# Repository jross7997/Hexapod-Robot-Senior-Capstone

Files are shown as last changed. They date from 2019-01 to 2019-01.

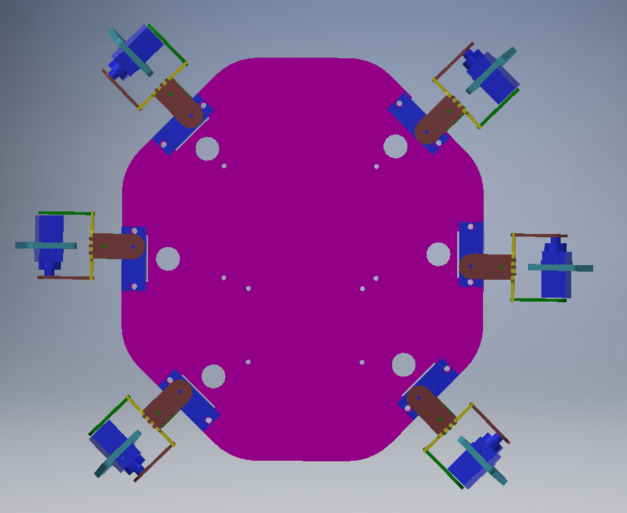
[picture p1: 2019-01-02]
Inventor Parts/Pictures of Parts/RobotTop.PNG

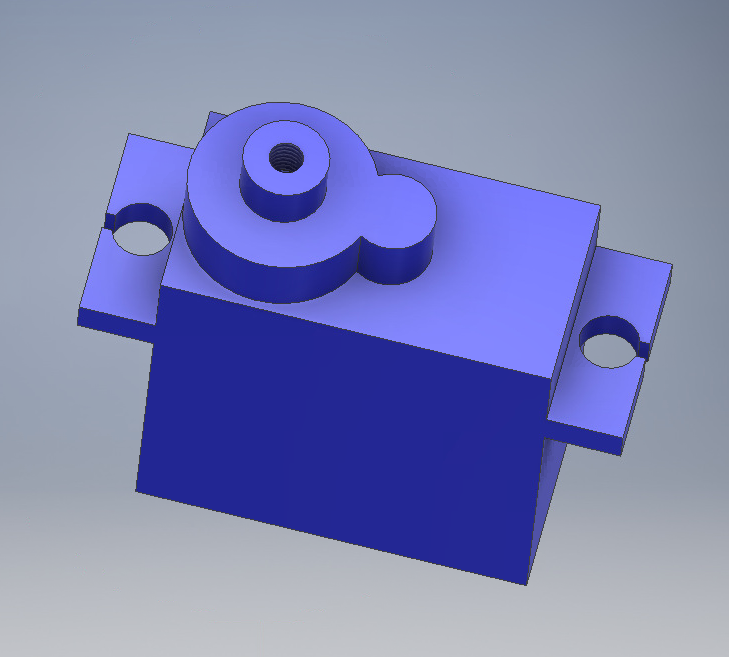
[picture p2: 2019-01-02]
Inventor Parts/Pictures of Parts/servo.PNG

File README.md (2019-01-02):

# Hexapod-Robot-Senior-Capstone
The collection of files created for my group's ECE 492: Capstone Design project

This contains files for the Fall 2018 Capstone Hexapod Walking Robot, built by Kara Fortunato, Justin Ross, and Justin Purtell.

The Projects folder contains the project folders for both the Tiva-C and the Node MCU. The Tiva-C folder is a Code Composer Studio Project.

The Source Code folder just contains the source code for each board. The Tiva-C source code contains a semi-extensive Servo library that was used to abstract away some complexities.

The Inventor Parts folder are all of the Autodesk Inventor parts that were modeled and later used for laser cutting.

The Final_Drawing.dwg is the actual file that a Universal Laser Systems Laser Cutter use to cut the parts.

There are also some instructions on how to connect to the Wifi-board

There was a vote to name it, and as voted on, her name is now Charlotte!
Enjoy!

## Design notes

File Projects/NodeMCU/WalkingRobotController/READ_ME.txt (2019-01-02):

This Code is meant for the NODEMCU 1.0
You need to install the board drivers into the Arduino IDE to get it to compile.
And to write to the NodeMCU, set the baud rate to 115200.

If you want to change the webpage that is displayed, I recommend making changes to the 
index.html file first, and then copying it's contents to the index.h file so that the new 
code is inbetween 
	const char MAIN_page[] PROGMEM = R"=====(
	<!--New/Modified HTML Code -->
	)=====";

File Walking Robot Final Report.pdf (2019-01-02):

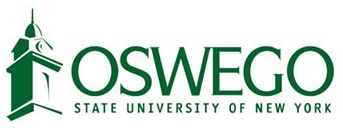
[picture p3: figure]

# SUNY Oswego

# Electrical and Computer Engineering Department

# ECE492

# Hexapod Walking Robot

By

# Kara Fortunato, Justin Ross, and Justin Purtell

## Supervisors

# Rachid Manseur and Marianne Hromalik

Submitted in Partial Fulfillment of the Requirement for the B.Sc. Degree, Electrical and Computer Engineering Department,

# Fall 2018

Project Abstract

Despite large efforts in modern engineering, one fact remains the same when it comes to robotic locomotion: legs and joints will always have a different set of rules than that of a wheeled vehicle when it comes to traversal over flat or rough terrain. A key consideration when designing a “legged” vehicle is how it keeps itself balanced without putting too much weight on one leg and collapsing during motion. In the field of robotics, especially, the ratio between a device’s sense of balance and ability to create forward motion in a way that keeps it grounded is highly important in many respects. The Walking Robot project aims to deliver a device that utilizes these concepts to develop a robot that can maintain its own sense of balance while having several degrees of freedom in movement to walk itself in various directions utilizing a series of controllable legs and joints.

Acknowledgment

All gratitude goes to the ECE department and our fellow colleagues for their advice and support throughout the development process. A special thank you to our advisors Dr. Rachid Manseur and Dr. Marianne Hromalik. Furthermore we would also like to acknowledge Dennis Quill for his involvement and advice.

Student Statement

Throughout the research and development process of this project, the designers, Kara Fortunato, Justin Ross, and Justin Purtell, have applied proper ethics to the design process and in selecting the final proposed design. The designers have held the safety of the public to be paramount and have addressed this in the design in all possible aspects.

Table of Contents

Project Abstract | 2
Acknowledgment | 2
Student Statement | 2
Table of Contents | 3
Figures & Tables List | 4
Problem Statement | 5
Problem Formulation | 5
Project Specifications | 6
Design & Analysis | 7
Number of Legs and Gait | 7
Texas Instruments TM4C123GH6PM | 8
Miuzei SG90 | 10
Individual Pieces of build | 11
NodeMCU V1 | 13
Circuit | 15
Final Build | 17
Standards used | 18
Cost Analysis/Bill of Materials | 18
Hazards & Failure Analysis | 19
ABET Learning Outcome | 20
Conclusions and Discussions | 22
Future Applications: | 22
Future Improvements: | 22
References | 23
Appendices | 24
A-1) Servo Code | 24
A-2) Servo Header File | 33
A-3) Legs Code | 35
A-4) Legs Header File | 41
A-5) UART Code | 42
A-6) UART Header File | 43

A-7) Main Code | 44
A-8) tm4c123gh6pm_startup_ccs.c | 47
A-9) NodeMCU Code | 54
A-10)Index.h | 56
A-11)Laser Cutting Diagram | 60
A-12) Wiring Diagram | 61
A-13) List of Servo to Pin Connections | 61
A-14) TM4C123GH6PM Features | 62
A-15) NodeMCU Specifications | 63
A-16) SG-90 Specifications | 64

Figures & Tables List

Figure 1: An example of the tripod gait | 8
Figure 2: The TM4C123GH6PM (Tiva-C) Microcontroller | 9
Figure 3: A Diagram of the PWM Generators | 9
Figure 4: Miuzei SG90 | 10
Figure 5: Frame Base | 11
Figure 6-8: Servo Mount, Cross-Connection Joint and Leg | 12
Figure 9: Joint and Leg Assembly | 13
Figure 10: The NodeMCU | 14
Figure 11: Web Interface | 14
Figure 12: Wiring Block Diagram | 15
Figure 13: Signal Wiring Diagram | 16
Figure 14: Servo Convention | 16
Figure 15-16: Inventor Assembly Front and Top | 17
Figure 17-19: Final Build Side, Top and Front | 17
Table 1: Student Cost Table
18
Table 2: Total Cost Table | 19

Problem Statement

The objectives of this design are to solve complex problems with robotic locomotion by developing a system in which a robot can walk on its own legs and joints while taking into consideration speed, balance, and aesthetic and ergonomic design.
As defined by a set of goals set by the assigning faculty, the design is also to be constructed of a sturdy material with a customized framework that could help accomplish these considerations with more ease than previous attempts at similar designs. This design is also to take into consideration the adjustments necessary to maintain the robots center of gravity always to allow the robot to balance properly during any direction of movement, as well as at any speed within reason. The customized aspect of this design should also give the robot a clean look about it, where the user should not have to worry about any harm coming to themselves or the robot’s construction while handling or assembling it.
Finally, the robot should be able to be controlled by some outside system where the user can have full control over various commands such as movement forward and backward, turning left or right, as well as any extra commands that can be programmed into the robot simply to make the robot more appealing to the user. This system could consist of an external controller or application that the user could manipulate in some way to achieve a desired command.

Problem Formulation

The issue of robotic movement is a popular topic amongst modern engineers. When you consider new systems that have been recently attempting to automate the workplace and leisure activities, the importance of robotics nowadays has become more paramount than ever. However, the importance of them operating as intended and being safe to operate are key stress factors in robotic design.
The idea of a walking robot has been established on some level within the electronics market already, therefore is an established concept with its own established drawbacks as well when considering scaling them up to a higher level of use. For example, if a working robot were to be used in the workplace, it would most likely be used to establish transport of materials or other product from one point of the building to another destination. This considered, the amount of engineering that must go into this type of product is very advanced because, the robot here not only has to manage to balance under the strain of its own weight; its center of gravity and weight distribution is also affected by any product that the robot may be carrying. Therefore, the necessary amount of design consideration changes considerably. On top of this, the engineer must consider the system that will be used to control the program that robot may run on if it is not entirely autonomous. This fine balance between software development and hardware engineering is part of what makes the field of robotics so complex.
In the case of the Walking Robot project, many of these issues were kept in mind throughout the design process due to the increasing need for these kinds of issues to be considered and solved by skilled engineers. For example, the need for it to balance and carry any weight that it must with the amount of hardware mounted to the frame has to be considered for the robot to perform proper movement. If this device were to be used to transport small goods, for example, this consideration would have to be made to account for the weight of anything it would carry as well to keep its center of gravity consistent with its direction of movement.
The control system of the Walking Robot project also has its own considerations towards these issues. The system that drives the robot should be not only simple enough for the user to operate with ease but, it should also allow as much control over the robot’s specific program as possible to allow the user to operate it accurately and efficiently in its intended application.

Project Specifications

The design of this project consists of many factors, from aspects such as the framework to programming the system to drive the robot’s movement. A strong blend of hardware and software knowledge were implemented to discover an efficient design that would accomplish the intended goals and stay within the constraints specified.
Firstly, the robot needed to be built from custom components that were designed to fit the purpose of the robot itself. The frame of the robot consisted of a series of legs, joints, and a base that could be easily connected and attached together to form the robot. This frame is also designed to house two microcontrollers as well as a series of servo motors that could be used to drive the joints and legs in various directions.

Secondly, a series of programs needed to be developed that could be used to control the servo motors in specific ways such that they could drive the robot in different directions based on how each of the legs and joints coordinated with each other in motion. These programs also take into consideration a method to operate the microcontroller remotely. This program should consist of a series of commands that coordinate with the microcontroller to allow it to activate different operations within the drive program based on user input. These inputs should include, at minimum, a forward drive, backward drive, and rotation left and right, as well as a stop
command. These commands should also have the option to run constantly until the user chooses to stop it.
In short, the agreed upon deliverables are listed below:
1. The robot needs to walk forwards, backwards, and turn left and right
2. The robot needs to maintain balance
3. The body of the robot needs to maintain integrity and look semi-professional

Design & Analysis

Number of Legs and Gait

The first thing that needed to be decided was the number of legs that would be used. There are advantages and disadvantages to each number of legs. For example, two legs would require less hardware than a four legged robot, but balancing on two legs is harder than on four. Since balance was the priority, 6 legs were selected. With a basic Tripod gait, at any given time, at least half of the legs are touching the ground, ensuring a balanced center of gravity. Other gaits for hexapods were considered, like the faster bipod gait, but none of them ensured the same balance that a tripod gait does. The minimum number of degrees of freedom required for a hexapod to use the tripod gait is 12 degrees. This directly translates to the number of servos that are required.

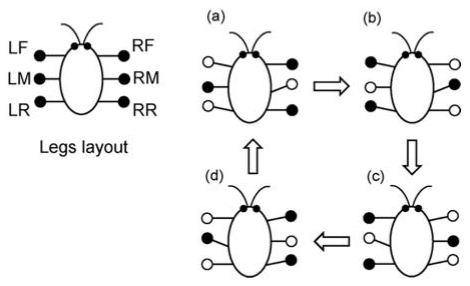
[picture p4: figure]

Figure 1: An example of the tripod gait The forward and backwards follow the Tripod Gait. Which means only three legs move at a time in a triangle shape. The front and back legs of one side along with the middle leg on the opposite side lift up, swing forward, drop down, and finally swing back. When backwards movement is needed, the legs will swing back instead of forward. Turning left and right follows a similar walk cycle. Three legs are on the ground at all times. When turning, the front and back legs swing forward, and the opposite middle leg will lift up and swing back. All three drop down and return back to the neutral standing position. Which way the robot turns is dependent on which sides legs swing forward, and which side swings back.

Texas Instruments TM4C123GH6PM
The microcontroller that was selected to drive the legs on the walking robot was the Texas Instruments TM4C123GH6PM or it was previously called the Tiva-C LaunchPad. The version that was used was still called the Tiva-C LaunchPad, but the new ones are identical. The Tiva-C is based off the 80 MHz ARM Cortex-M4F chipset and has 35 available GPIO pins [2]. It has many available accessories, but the one that was most important to this project was the 16 independent PWM outputs that are generated from two separate PWM modules, each with 4 PWM generators.

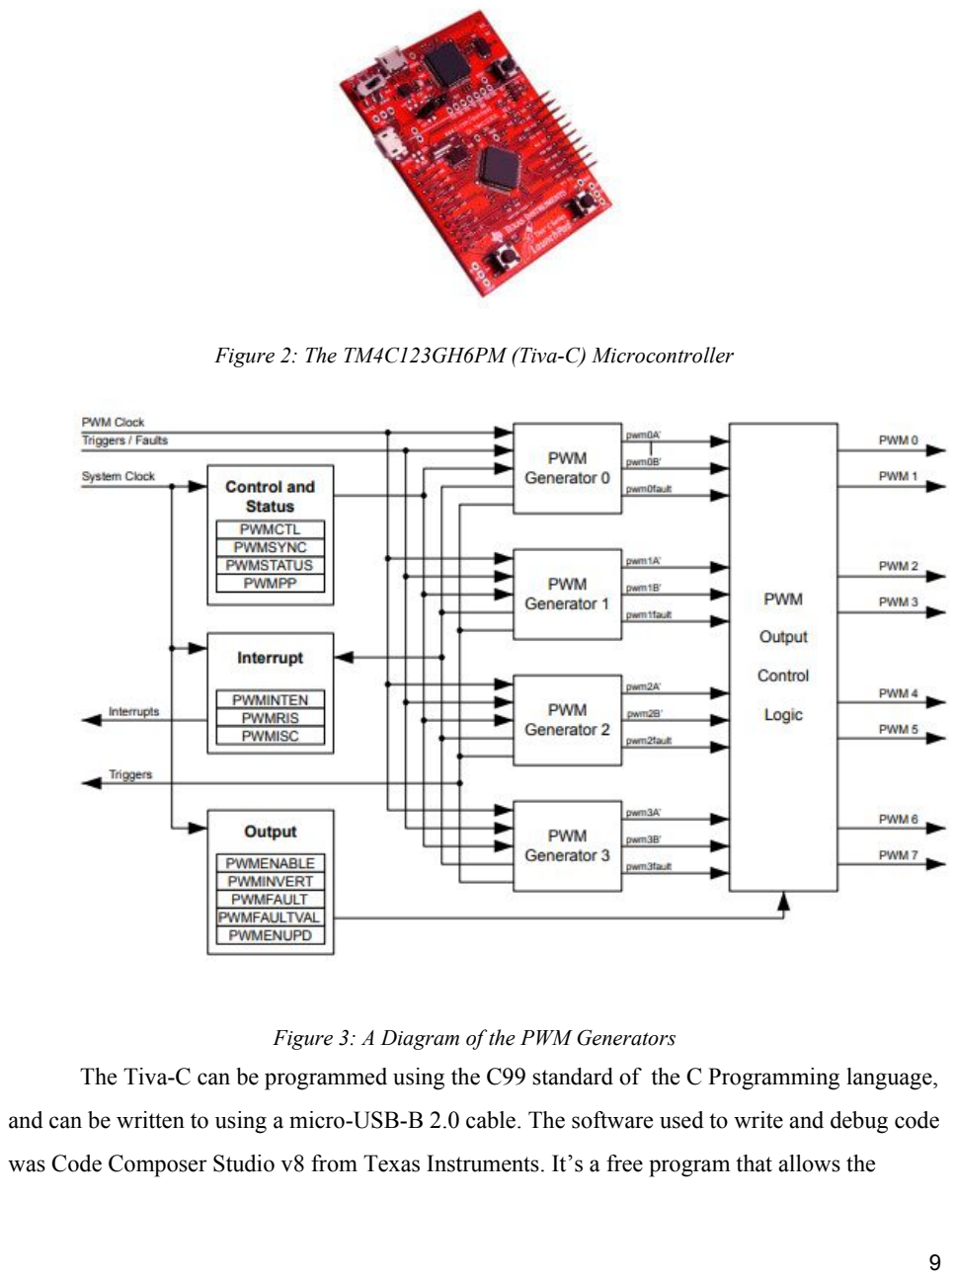
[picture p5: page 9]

Figure 2: The TM4C123GH6PM (Tiva-C) Microcontroller

Figure 3: A Diagram of the PWM Generators The Tiva-C can be programmed using the C99 standard of the C Programming language, and can be written to using a micro-USB-B 2.0 cable. The software used to write and debug code was Code Composer Studio v8 from Texas Instruments. It’s a free program that allows the composition and debugging of code for the Tiva-C, among other Texas Instruments microcontrollers.
Texas Instruments had created a library called “driverlib” that has a variety of register level abstractions that makes programming the Tiva-C a bit easier. Instead of moving individual bits in registers, higher level functions can be called to make the readability of the code easier. But, if necessary, the ability to move individual bits in registers is still available to the user.
The Tiva-C was chosen over other available microcontrollers for two main reasons, versatility and availability. As previously discussed, the Tiva-C has a load of available functions, so the potential for the addition of more features is possible. There was also more than enough PWM pins for the robot. The Tiva-C was also available for free from the ECE department, which helped inform our decision.

Miuzei SG90

It was decided early on that a design goal was to minimize the weight of the walker, so a micro servo form factor was selected. The next thing that was considered was the type of gearing, metal or plastic. The metal gearing is known to be more durable, but they are heavier and more expensive than plastic. Considering this, the Miuzei SG90 micro servos were selected. They have plastic gearing and were lighter and significantly cheaper than the metal counterparts. Twelve SG90’s were used, and they are controlled with a 55 Hz PWM pulse train from the Texas Instruments TM4C123GH6PM microcontroller. The motors have a 120° range of motion, which was more than enough to ensure movement [3].

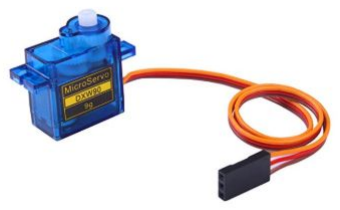
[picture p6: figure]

Figure 4: Miuzei SG90

Individual Pieces of build
The frame is designed using the 3-dimensional computer aided design (CAD) software AutoDesk Inventor. The components are laser-cut from acrylic sheets to ensure that the design was not only pin-point accurate but also sturdy enough to hold up during the next phases. The use of a 3D printer was considered, but it was determined that laser cutting would be a better approach for this project. The ECE department has access to a Universal laser systems laser cutter, making it easy for students to create and cut components without going through a third party. 3D components also cost money according to how long the project takes and how much material is used. Laser cutting has no cost except for the acrylic, which is provided by the department. Additionally, laser cutting is much faster than 3D printing. The entire project takes less than ten minutes to laser cut while a 3D printer might take hours. The fast cutting time allows for models to be adjusted or completely reprinted completely. This is necessary because the robot was completely redesigned several times.
The first part of the frame to be considered was the shape and construction of the base. For this, an octagonal shape is used to allow the robot to consist of 6 legs, 3 on the left side and 3 on the right side, as well as including ports for all the necessary hardware mounting. Holes were made in the base to hold the servos and so that the microcontroller circuit could be mounted.

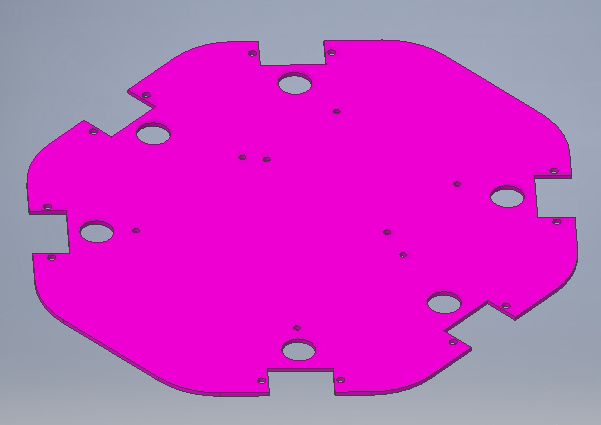
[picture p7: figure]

Figure 5: Frame Base

Next, the legs and joints are designed such that they could hold the servo motors in place and use them for movement while remaining locked to the joints and base by mounting screws and acrylic epoxy. The legs are cut with a concave, pointed “toe” that are coated with a rubber tip such that they could have a strong connection with the ground without slipping. The joints each have cut-out slots that connect each of the joint types to one another. A screw-mounted joint is also used on each side of the servos on the legs and on the base to help lock them in place during movement and keep them connected to the frame.

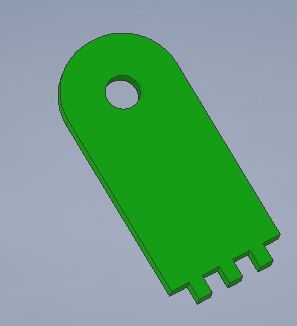
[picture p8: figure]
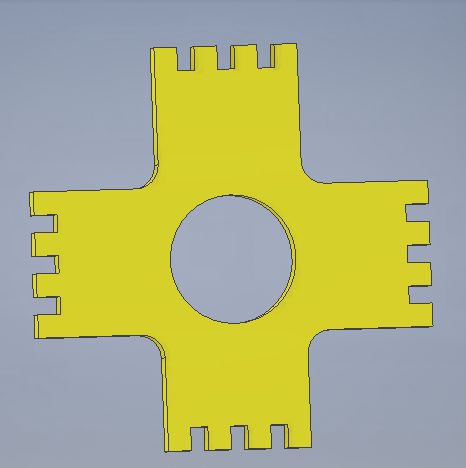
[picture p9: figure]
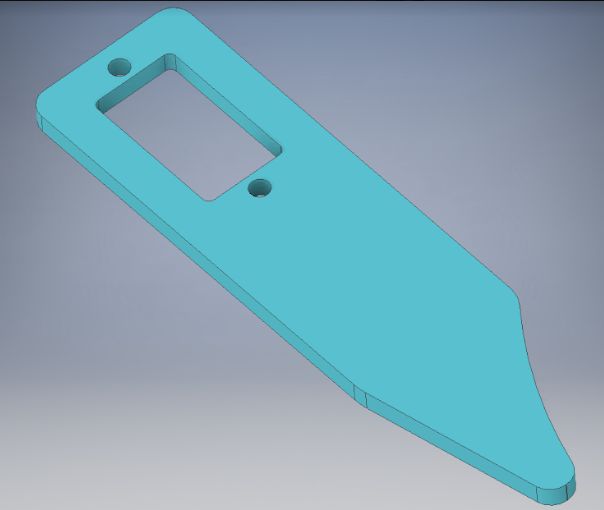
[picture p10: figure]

Figure 6: Servo Mount | Figure 7: Cross Connection Joint | Figure 8: Leg

Once assembled, each leg joint consisted of one cross connection joint, four servo mounts, one leg, and two servos. Each servo was given a number to be referred to. The servo that would be connected to the based was dubbed servo “one” while the servo directly connected to the leg was called servo “two”. This allowed for each servo to be distinguished when the circuit was being built. The final leg joint assembly can be seen in the following figure.

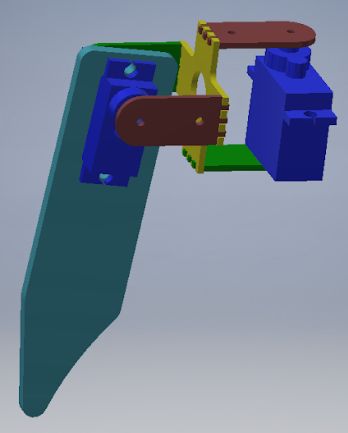
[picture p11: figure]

Figure 9: Joint and Leg Assembly

NodeMCU V1

To control the robot, a method of control needs to be selected. Wireless control was chosen because of accessibility. Anyone with a smart device should be able to have access. To accomplish this, the NodeMCU V1 was used. It is a WiFi-enabled microcontroller that uses the ESP8266MOD chip and can broadcast WiFi in accordance to the IEEE 802.11 b/g/n standard [4]. The NodeMCU has the capability to act as a soft access point that can serve web pages and was programmed using a modified version of C++ in the Arduino IDE. The NodeMCU also supports Lua scripting, but there were issues with the serial connection when the firmware is set for Lua scripting. The only way found to ensure a reliable experience was the use of the Arduino IDE. The NodeMCU was chosen over a Bluetooth module because of the accessibility it provides. Any WiFi enabled device can access and use the walking robot, but a Bluetooth module would require either an OS specific app, or the use of a generic Bluetooth command line.

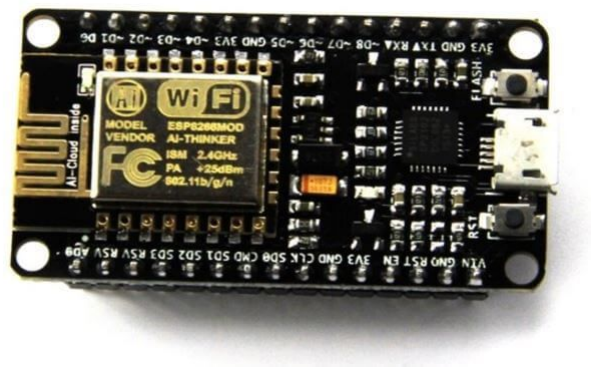
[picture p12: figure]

Figure 10: The NodeMCU
To coordinate with the WiFi module, the program allows the user to connect to the module’s IP address where a web application is loaded that allows the module to communicate with the microcontroller to activate various methods in the servo program based on user command. The application consists of commands including, forward, backward, rotate left, rotate right, stop, wave, continuous operation, and a speed toggle. The web application was written using HTML and AJAX (Asynchronous JavaScript and XML). These commands interact with the TM4C123GH6PM via a UART bridge at a 115200 baud rate, which cause an interrupt, and the previous command is saved to a global variable. Each possible command is mapped to a specific movement function.

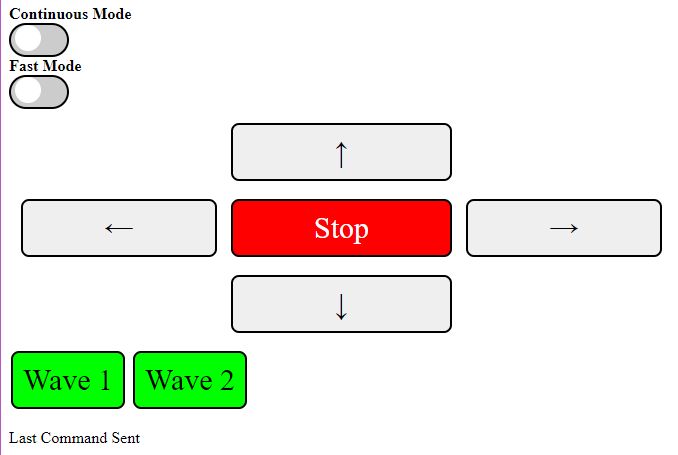
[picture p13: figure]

Figure 11: Web Interface

Circuit

To tie all the components together, a circuit needs to be constructed and soldered together. Each of the twelve servos need to be connected to its respective PWM pin on the Tiva
C. The UART bridge between the Tiva-C and the NodeMCU needs to be put in place. And each of the components need to be powered by an external benchtop power supply. The power supply’s point of entry is the two wires attached to a switch to turn the circuit on or off.

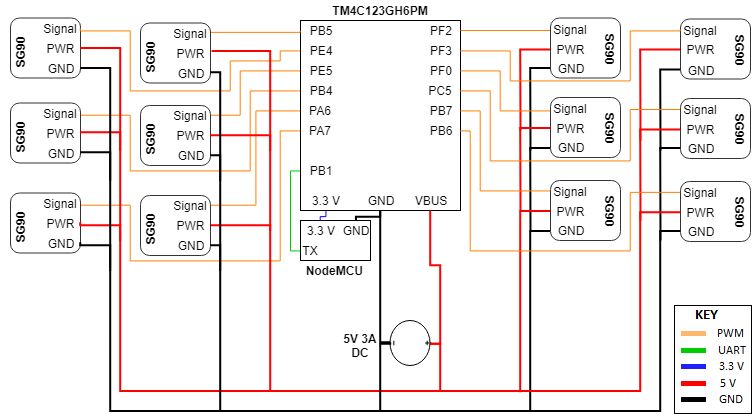
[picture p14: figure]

Figure 12: Wiring Block Diagram

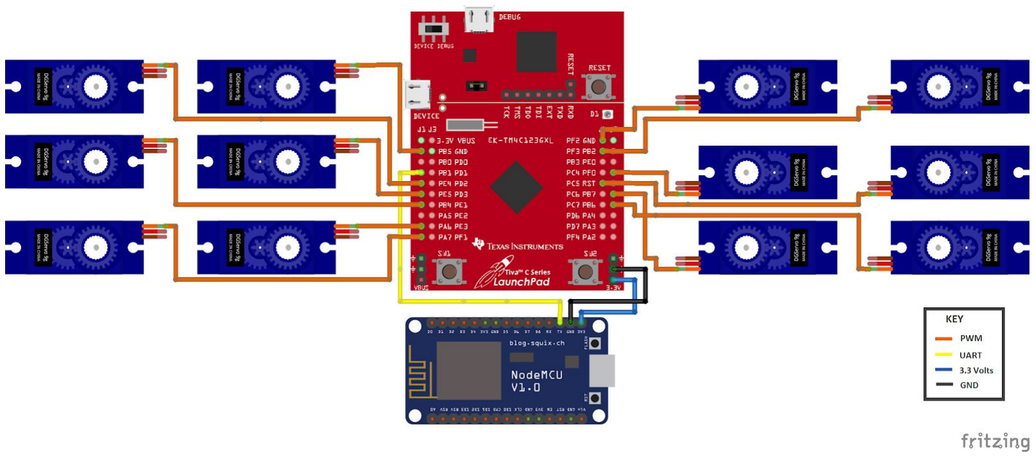
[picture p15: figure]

Figure 13: Signal Wiring Diagram To ensure consistency throughout all aspects of the project, a convention for the legs in terms of the circuit positioning needed to be determined. The base was divided into 3 sections; Front, Middle, and Back. The left side has 6 servos, and the right side has 6 servos. The servos closest to the body are denoted as a servo 1, and the ones on the legs servo 2’s. Knowing what side, left or right, and what third of the base the servo is on, the servo number can quickly be determined. The front needed to be distinct to differentiate the left from the right side and the back from the front. The way that the front was denoted was by the row of googly eyes.

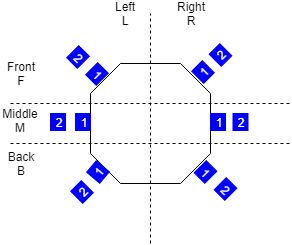
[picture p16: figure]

Figure 14: Servo conventions The physical construction of the circuit was simply done with a 6x8 cm and a 4x6 cm double-sided prototyping PCB. The NodeMCU was placed into soldered female headers on the 4x6 cm board, and the Tiva-C was placed onto soldered male headers on the 6x8cm board. The connections are as shown in the figures above. There were some obstacles that were faced with the soldering, most of which come from inexperience. The biggest issue come from the nature of a solid core wire. Those wires are much more rigid than a braided wire, and are very easy to break.
The final build consisted of six legs and their corresponding joints, as well as one base. Servo “one” is the servo that is directly connected to the base while servo “two” connects to the leg. The final necessary design to be implemented is the mounted PCB. Mounted to the PCB are the WiFi module, the microcontroller, and a switch that can be used to turn the robot on and off. The PCB is then mounted onto the frame’s base using through-hole standoffs of size M2. These components are soldered to the prototyping PCB, as well as each of the PWM ports and WiFi module ports to allow all of the signals to be properly routed to their destinations. To power the robot, a lab bench power supply was set to 5 Volts and 3 Amps and then attached directly to the switch.

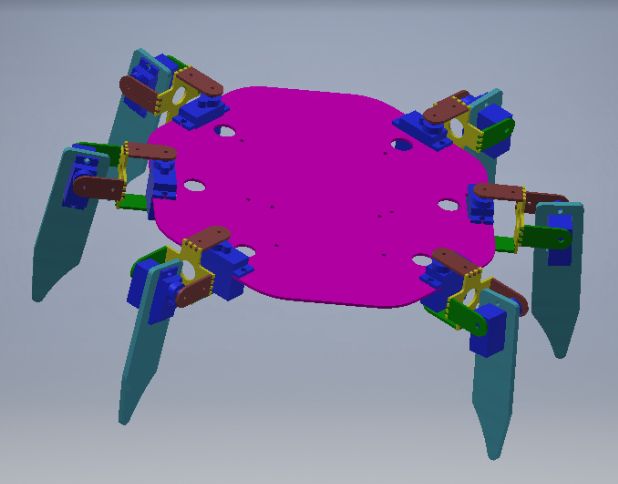
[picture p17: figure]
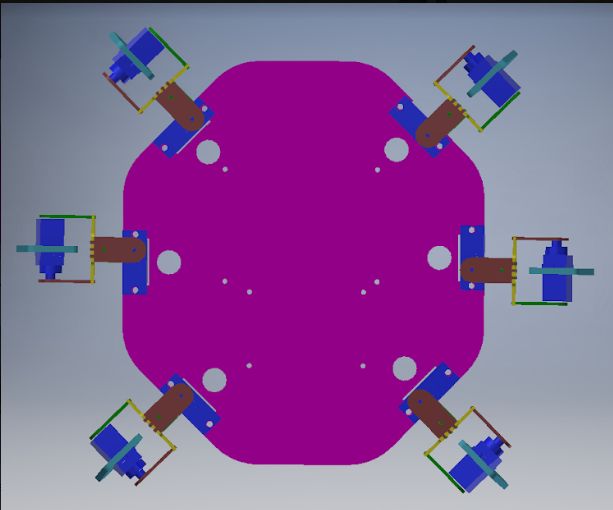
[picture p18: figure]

Figure 15: Inventor Assembly Front | Figure 16: Inventor Assembly Top

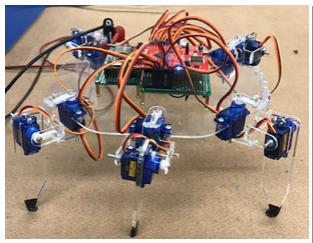
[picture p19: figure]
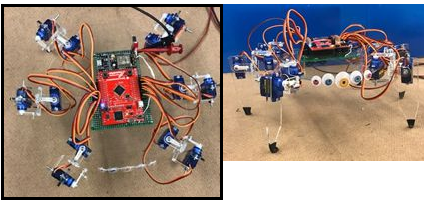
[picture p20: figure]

Figure 17: Final Build (Side) | Figure 18: Final Build (Top) | Figure 19: Final Build (Front)

Standards used
ISO/IEC 9899:1999 for C programming language IEEE 802.11 b/g/n for Wireless Communications Universal Asynchronous Receiver/Transmitter Pulse Width Modulation

Cost Analysis/Bill of Materials

The cost to build the device takes into consideration every individual component and necessary material that was used to complete each step of the design from the planning phase up to the build and testing phases. The total bill of materials used to develop the device is included below.

Table 1: Total Bill of Materials Per-Component

Component/ Material | Quantity | Vendor | Cost ($)
Miuzei SG90 Servo Motors | 12 (+ Extras) | Amazon.com (https://www.amazon.com/Micro-Helicopter-Airplane-Remote-Control/dp/B072V529YD) | 34.58
TM4C123GH6PM Microcontroller | 1 | Mouser (https://www.mouser.com/ProductDetail/Texas-Instruments/EK-TM4C123GXL?qs=TB%2FQ0sBK%2FGefKGr%252bQsiJWQ%3D%3D) | 13.45
Node-MCU V1 Wifi Module | 1 | Amazon.com (https://www.amazon.com/HiLetgo-Internet-Development-Wireless-Micropython/dp/B010O1G1ES?s=electronics) | 8.39
4-40 Machine Bolts and Nuts | 30 each (+ Extras) | Raby’s Ace | 12.44
6 x 8 cm Prototyping PCB | 1 (+ Extras) | Amazon.com (https://www.amazon.com/Double-Side-Prototype-Universal-Printed-Circuit/dp/B0147YM3DG) | 5.99
4 x 6 cm Prototyping PCB | 1(+ Extras) | Amazon.com (https://www.amazon.com/Universal-Protoboard-Prototyping-Printed-Circuit/dp/B06XTPGBS5) | 6.99
M2 Standoff Kit | 1 | Amazon.com (https://www.amazon.com/d/Tile-Spacers/Hilitchi-120pcs-Female-Standoff-Assortment/B018C19KOA) | 8.99
1/16 in Thick 16x24 in Acrylic Sheet | 1 | ePlastics.com (https://www.eplastics.com/sheets/acrylic-plexiglass/plexiglass-acrylic-sheets-clear-SAMPLE-ACRYCLRTHIN-CLEAR) | 8.49
1/8 in Thick 16x24 in Acrylic Sheet | 1 | ePlastics.com (https://www.eplastics.com/SAMPLE-ACRYCLRTHICK-CLEAR) | 21.69
Two-Part Quick Setting Epoxy | 1 | Walmart (https://www.walmart.com/ip/J-B-Weld-50132-PlasticWeld-Quick-Setting-Epoxy-Syringe-Dries-Off-White-25-ml/725449397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) | 5.35
3/8 in Heat Shrink Tubing | 1 | Jameco (https://www.jameco.com/z/FIT-221B-3-8-BK100-VP-Heat-Shrink-Tubing-Fit-221B-3-8-Black-4-Feet-Black-Polyolefin-Tubing_419223.html) | 1.75
Colored Googly Eyes | 1 | Dollar Tree | 1.00
Total Cost | | | 129.11

The total cost to the students with the resources that SUNY Oswego’s ECE Department provides.

Table 2: Total Student Cost Per-Component

Component/ Material | Quantity | Vendor | Cost ($)
Miuzei SG90 Servo Motors | 12 (+ Extras) | Amazon.com (https://www.amazon.com/Micro-Helicopter-Airplane-Remote-Control/dp/B072V529YD) | 34.58
TM4C123GH6PM Microcontroller | 1 | Provided | --
Node-MCU V1 Wifi Module | 1 | Amazon.com (https://www.amazon.com/HiLetgo-Internet-Development-Wireless-Micropython/dp/B010O1G1ES?s=electronics) | 8.39
4-40 Machine Bolts and Nuts | 30 each (+ Extras) | Raby’s Ace | 12.44
6 x 8 cm Prototyping PCB | 1 | Provided | --
4 x 6 cm Prototyping PCB | 1 | Provided | --
M2 Standoff Kit | 1 | Amazon.com (https://www.amazon.com/d/Tile-Spacers/Hilitchi-120pcs-Female-Standoff-Assortment/B018C19KOA) | 8.99
1/16 in Thick 16x24 in Acrylic Sheet | 1 | Provided | --
1/8 in Thick 16x24 in Acrylic Sheet | 1 | Provided | --
Two-Part Quick Setting Epoxy | 1 | Walmart (https://www.walmart.com/ip/J-B-Weld-50132-PlasticWeld-Quick-Setting-Epoxy-Syringe-Dries-Off-White-25-ml/725449397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) | 5.35
3/8 in Heat Shrink Tubing | 1 | Provided | --
Colored Googly Eyes | 1 | Dollar Tree | 1.00
Total Cost | | | 70.75

The operational costs of the walking robot are only that of the cost of electricity that powers the bench power supply.

Hazards & Failure Analysis

As with any solution in development to solve a set of problems, it is the responsibility of the designing engineer to uphold the safety of the public and environment when making any design decision that affects the end-product and how it will be used or perceived by consumers.

Safety was a key feature in the design of the walking robot. There are no sharp edges on the acrylic pieces, and the exposed screws have all be covered with hot glue to prevent any injuries.
The potential for failure is greatest in the joints. Each of the joints is held together with glue, which breaks under high stress.

ABET Learning Outcome

Throughout this project, the take-away from the design process consists of applied knowledge of many of the outcomes outlined by ABET for engineering students required to train as a professional. Various aspects of this design and development process coordinate with these outcomes in many ways.
Engineering Learning Outcomes

### 1. an ability to identify, formulate, and solve complex engineering problems by applying

principles of engineering, science, and mathematics
a. The ECE capstone class is design to get students to identify and solve a problem. In this situation, the problem was to create a walking robot. This was solved using principles and skill involved in math, science, and engineering. These skills included soldering, coding and circuitry among countless others. Without the knowledge gained in classes from the ECE major it would have been nearly impossible to complete this project.
2. an ability to apply engineering design to produce solutions that meet specified needs with consideration of public health, safety, and welfare, as well as global, cultural, social, environmental, and economic factors
a. Several parts of this project could be considered dangerous if not taken care of. For example, a large amount of voltage could be considered dangerous. This robot runs on 5v, a relatively low amount of voltage which is safe for those working with the project. Several screws are sharp and could conflict pain. These screws have been either filed down or had caps put over them to ensure the safety of those near it. The safety of those working on the project and others who may come in contact it was an important of this project and was considered

### 3. an ability to communicate effectively with a range of audiences

a. The ability to communicate with a range of audiences was very important in this project. Not only did the team have to communicate with each other, but reports had to be written at every step which explained the project to those who had no part in it. The group made several reports, including this final report, to explain the project in a manner that can be understood by a large range of audiences.
4. an ability to recognize ethical and professional responsibilities in engineering situations and make informed judgments, which must consider the impact of engineering solutions in global, economic, environmental, and societal contexts
a. This project can be built upon to eventually create a robot that could help the world. However, as the project is now, the ability to make informed judgements considering global and societal contexts was irrelevant.
5. an ability to function effectively on a team whose members together provide leadership, create a collaborative and inclusive environment, establish goals, plan tasks, and meet objectives
a. One of the very first things that was completed on this project was the creation of a task list. This included each step of the process that was to be completed. The use of a task list allowed the group to create and complete goals. The group that designed this robot consisted of three group members. Each group member worked towards one cohesive finished project but took on smaller tasks to get to that goal. For example, one group member was working on the code itself while another soldered together a circuit for the code to run on. This allowed for the project to be completed in a timely manner. The ability to function well on a team and to follow a set task list allowed for the project to be completed effectively.

### 6. an ability to develop and conduct appropriate experimentation, analyze and interpret

data, and use engineering judgment to draw conclusions
a. Experimentation was used at every step of the process in building this robot. The laser printed legs were one part of the project that took a lot of experimentation.

Initially, the legs were very tall with one point at the bottom. This leg was glued to a servo for initial testing. This leg design did not allow the robot to stand on its own because it was too tall and because the single point caused the leg to slip out from underneath the robot. The leg was then modified to hold one servo near the top, and was shortened in length. This allowed a better connection between the leg and the servo. Eventually, after much experimentation and roughly 8 redesign, the leg which is used in the final project was created. The ability to experiment, gather data, and adjust the project accordingly was very important for this project.

### 7. an ability to acquire and apply new knowledge as needed, using appropriate learning

strategies
a. Through code composer labs, the group was able to learn the necessary
commands to program the Tiva-C microcontroller. Other knowledge that may have been needed was requested by faculty or researched separately.

Conclusions and Discussions

The design goal of this walking robot was to walk forward, backward, turn left and right all while keeping its balance. That goal was accomplished, and even expanded upon. For example, the introduction of a WiFi based control system and the two waving functions.

Future Applications:

The design as it currently stands is intended for educational and entertainment uses.

Future Improvements:

1. Time and budget did not permit the inclusion of a battery system to make the system more portable. The use of a battery with a high energy density but a low weight would be ideal, something like a Lithium-Ion or Lithium-Polymer battery pack would work well.
2. Editing the movement methods to make the robot walk more naturally. It currently walks in a very robotic and rigid way. A basic kinematic model could be used to speed up the process of modifying the movement methods.

3. The joints between each servo on the leg are currently held together with glue, which is prone to breaking. A redesign of the joints such that they can be held together with traditional mounting hardware like nuts and bolts would eliminate the problem.

References

[1]B. Baxter, “Tripod-walking Gait,” The Tripod Gait as a Model for Robots. [Online]. Available: https://tripodgaitasamodelforrobots.weebly.com/tripod-walking-gait.html.
[2]“Tiva™ TM4C123GH6PM Microcontroller,” ti.com. [Online]. Available: http://www.ti.com/lit/ds/symlink/tm4c123gh6pm.pdf.
[3]“SG90 Data Sheet.” [Online]. Available: http://www.ee.ic.ac.uk/pcheung/teaching/DE1_EE/stores/sg90_datasheet.pdf.
[4]“NodeMCU ESP8266 ESP-12E WiFi Development Board.” [Online]. Available: https://einstronic.com/wp-content/uploads/2017/06/NodeMCU-ESP8266-ESP-12E-Catalogue.pdf.

Appendices

A-1) Servo Code

*
* servo.c
* Library based off the TIVA C workshop to control the SG90 micro servos *
* Created on: Sep 27, 2018
* Author: jross5
*/

#include <stdint.h>

#include <stdbool.h>

#include "inc/hw_memmap.h" #include "inc/hw_types.h"

#include "driverlib/sysctl.h" #include "driverlib/gpio.h" #include "driverlib/debug.h" #include "driverlib/pwm.h" #include "driverlib/pin_map.h" #include "inc/hw_gpio.h"

#include "driverlib/rom.h"

#define PWM_FREQUENCY 55

uint32_t getPWMFrequency(){
| return PWM_FREQUENCY;
}

void delayMS(uint32_t ms)
{
| SysCtlDelay((SysCtlClockGet() / (3 * 1000)) * ms);
}

uint32_t getPWMClock(){
| return (SysCtlClockGet() / 64);
}

uint32_t getLoad(uint32_t ui32PWMClock, uint32_t ui32PWMFreq){
| return ((ui32PWMClock / ui32PWMFreq) - 1);
}
void PWM_Enable(){
| SysCtlPWMClockSet(SYSCTL_PWMDIV_64); SysCtlPeripheralEnable(SYSCTL_PERIPH_PWM1); SysCtlPeripheralEnable(SYSCTL_PERIPH_PWM0);

}
void GPIOPWM_Enable(){
| SysCtlPeripheralEnable(SYSCTL_PERIPH_GPIOA); SysCtlPeripheralEnable(SYSCTL_PERIPH_GPIOB); SysCtlPeripheralEnable(SYSCTL_PERIPH_GPIOC);

SysCtlPeripheralEnable(SYSCTL_PERIPH_GPIOD); SysCtlPeripheralEnable(SYSCTL_PERIPH_GPIOE); SysCtlPeripheralEnable(SYSCTL_PERIPH_GPIOF);
}

//------------------------------------------------------------------------------------------------------------
//M0 Initilization Methods //-------------------------------------------------------------------------------------------------------------
void M0PWM0_Init(uint32_t ui32Load){
GPIOPinTypePWM(GPIO_PORTB_BASE, GPIO_PIN_6); GPIOPinConfigure(GPIO_PB6_M0PWM0); PWMGenConfigure(PWM0_BASE, PWM_GEN_0, PWM_GEN_MODE_DOWN); PWMGenPeriodSet(PWM0_BASE, PWM_GEN_0, ui32Load); PWMOutputState(PWM0_BASE, PWM_OUT_0_BIT, true); PWMGenEnable(PWM0_BASE, PWM_GEN_0);
}
void M0PWM1_Init(uint32_t ui32Load){ GPIOPinTypePWM(GPIO_PORTB_BASE, GPIO_PIN_7); GPIOPinConfigure(GPIO_PB7_M0PWM1); PWMGenConfigure(PWM0_BASE, PWM_GEN_0, PWM_GEN_MODE_DOWN); PWMGenPeriodSet(PWM0_BASE, PWM_GEN_0, ui32Load); PWMOutputState(PWM0_BASE, PWM_OUT_1_BIT, true); PWMGenEnable(PWM0_BASE, PWM_GEN_0);
}
void M0PWM2_Init(uint32_t ui32Load){ GPIOPinTypePWM(GPIO_PORTB_BASE, GPIO_PIN_4); GPIOPinConfigure(GPIO_PB4_M0PWM2); PWMGenConfigure(PWM0_BASE, PWM_GEN_1, PWM_GEN_MODE_DOWN); PWMGenPeriodSet(PWM0_BASE, PWM_GEN_1, ui32Load); PWMOutputState(PWM0_BASE, PWM_OUT_2_BIT, true); PWMGenEnable(PWM0_BASE, PWM_GEN_1);
}
void M0PWM3_Init(uint32_t ui32Load){ GPIOPinTypePWM(GPIO_PORTB_BASE, GPIO_PIN_5); GPIOPinConfigure(GPIO_PB5_M0PWM3); PWMGenConfigure(PWM0_BASE, PWM_GEN_1, PWM_GEN_MODE_DOWN); PWMGenPeriodSet(PWM0_BASE, PWM_GEN_1, ui32Load); PWMOutputState(PWM0_BASE, PWM_OUT_3_BIT, true); PWMGenEnable(PWM0_BASE, PWM_GEN_1);
}
void M0PWM4_Init(uint32_t ui32Load){ GPIOPinTypePWM(GPIO_PORTE_BASE, GPIO_PIN_4); GPIOPinConfigure(GPIO_PE4_M0PWM4); PWMGenConfigure(PWM0_BASE, PWM_GEN_2, PWM_GEN_MODE_DOWN); PWMGenPeriodSet(PWM0_BASE, PWM_GEN_2, ui32Load); PWMOutputState(PWM0_BASE, PWM_OUT_4_BIT, true); PWMGenEnable(PWM0_BASE, PWM_GEN_2);
}
void M0PWM5_Init(uint32_t ui32Load){ GPIOPinTypePWM(GPIO_PORTE_BASE, GPIO_PIN_5); GPIOPinConfigure(GPIO_PE5_M0PWM5); PWMGenConfigure(PWM0_BASE, PWM_GEN_2, PWM_GEN_MODE_DOWN);

PWMGenPeriodSet(PWM0_BASE, PWM_GEN_2, ui32Load); PWMOutputState(PWM0_BASE, PWM_OUT_5_BIT, true); PWMGenEnable(PWM0_BASE, PWM_GEN_2);
}
void M0PWM6_Init(uint32_t ui32Load){ GPIOPinTypePWM(GPIO_PORTC_BASE, GPIO_PIN_4); GPIOPinConfigure(GPIO_PC4_M0PWM6); PWMGenConfigure(PWM0_BASE, PWM_GEN_3, PWM_GEN_MODE_DOWN); PWMGenPeriodSet(PWM0_BASE, PWM_GEN_3, ui32Load); PWMOutputState(PWM0_BASE, PWM_OUT_6_BIT, true); PWMGenEnable(PWM0_BASE, PWM_GEN_3);
}
void M0PWM7_Init(uint32_t ui32Load){ GPIOPinTypePWM(GPIO_PORTC_BASE, GPIO_PIN_5); GPIOPinConfigure(GPIO_PC5_M0PWM7); PWMGenConfigure(PWM0_BASE, PWM_GEN_3, PWM_GEN_MODE_DOWN); PWMGenPeriodSet(PWM0_BASE, PWM_GEN_3, ui32Load); PWMOutputState(PWM0_BASE, PWM_OUT_7_BIT, true);
PWMGenEnable(PWM0_BASE, PWM_GEN_3);
}

//------------------------------------------------------------------------------------------------------------
//M1 Initilization Methods //-------------------------------------------------------------------------------------------------------------
void M1PWM0_Init(uint32_t ui32Load){
GPIOPinTypePWM(GPIO_PORTD_BASE, GPIO_PIN_0); GPIOPinConfigure(GPIO_PD0_M1PWM0); PWMGenConfigure(PWM1_BASE, PWM_GEN_0, PWM_GEN_MODE_DOWN); PWMGenPeriodSet(PWM1_BASE, PWM_GEN_0, ui32Load); PWMOutputState(PWM1_BASE, PWM_OUT_0_BIT, true); PWMGenEnable(PWM1_BASE, PWM_GEN_0);
}
void M1PWM1_Init(uint32_t ui32Load){ GPIOPinTypePWM(GPIO_PORTD_BASE, GPIO_PIN_1); GPIOPinConfigure(GPIO_PD1_M1PWM1); PWMGenConfigure(PWM1_BASE, PWM_GEN_0, PWM_GEN_MODE_DOWN); PWMGenPeriodSet(PWM1_BASE, PWM_GEN_0, ui32Load); PWMOutputState(PWM1_BASE, PWM_OUT_1_BIT, true); PWMGenEnable(PWM1_BASE, PWM_GEN_0);
}
void M1PWM2_Init(uint32_t ui32Load){ GPIOPinTypePWM(GPIO_PORTA_BASE, GPIO_PIN_6); GPIOPinConfigure(GPIO_PA6_M1PWM2); PWMGenConfigure(PWM1_BASE, PWM_GEN_1, PWM_GEN_MODE_DOWN); PWMGenPeriodSet(PWM1_BASE, PWM_GEN_1, ui32Load); PWMOutputState(PWM1_BASE, PWM_OUT_2_BIT, true); PWMGenEnable(PWM1_BASE, PWM_GEN_1);
}
void M1PWM3_Init(uint32_t ui32Load){ GPIOPinTypePWM(GPIO_PORTA_BASE, GPIO_PIN_7); GPIOPinConfigure(GPIO_PA7_M1PWM3); PWMGenConfigure(PWM1_BASE, PWM_GEN_1, PWM_GEN_MODE_DOWN);

PWMGenPeriodSet(PWM1_BASE, PWM_GEN_1, ui32Load); PWMOutputState(PWM1_BASE, PWM_OUT_3_BIT, true); PWMGenEnable(PWM1_BASE, PWM_GEN_1);
}
void M1PWM4_Init(uint32_t ui32Load){ GPIOPinTypePWM(GPIO_PORTF_BASE, GPIO_PIN_0); GPIOPinConfigure(GPIO_PF0_M1PWM4); PWMGenConfigure(PWM1_BASE, PWM_GEN_2, PWM_GEN_MODE_DOWN); PWMGenPeriodSet(PWM1_BASE, PWM_GEN_2, ui32Load); PWMOutputState(PWM1_BASE, PWM_OUT_4_BIT, true); PWMGenEnable(PWM1_BASE, PWM_GEN_2);
}
void M1PWM5_Init(uint32_t ui32Load){ GPIOPinTypePWM(GPIO_PORTF_BASE, GPIO_PIN_1); GPIOPinConfigure(GPIO_PF1_M1PWM5); PWMGenConfigure(PWM1_BASE, PWM_GEN_2, PWM_GEN_MODE_DOWN); PWMGenPeriodSet(PWM1_BASE, PWM_GEN_2, ui32Load); PWMOutputState(PWM1_BASE, PWM_OUT_5_BIT, true); PWMGenEnable(PWM1_BASE, PWM_GEN_2);
}
void M1PWM6_Init(uint32_t ui32Load){ GPIOPinTypePWM(GPIO_PORTF_BASE, GPIO_PIN_2); GPIOPinConfigure(GPIO_PF2_M1PWM6); PWMGenConfigure(PWM1_BASE, PWM_GEN_3, PWM_GEN_MODE_DOWN); PWMGenPeriodSet(PWM1_BASE, PWM_GEN_3, ui32Load); PWMOutputState(PWM1_BASE, PWM_OUT_6_BIT, true); PWMGenEnable(PWM1_BASE, PWM_GEN_3);
}
void M1PWM7_Init(uint32_t ui32Load){ GPIOPinTypePWM(GPIO_PORTF_BASE, GPIO_PIN_3); GPIOPinConfigure(GPIO_PF3_M1PWM7); PWMGenConfigure(PWM1_BASE, PWM_GEN_3, PWM_GEN_MODE_DOWN); PWMGenPeriodSet(PWM1_BASE, PWM_GEN_3, ui32Load); PWMOutputState(PWM1_BASE, PWM_OUT_7_BIT, true);
PWMGenEnable(PWM1_BASE, PWM_GEN_3);
}
//------------------------------------------------------------------------------------------------------------
//M0 Position Methods
//-------------------------------------------------------------------------------------------------------------
//M0 PWM0 Pin PB6 position method
void M0PWM0_PositionServo(uint8_t ui8Degrees, uint32_t ui32Load) // Servo position from 0 to 120 degrees
{
uint8_t ui8Adjust;

if (ui8Degrees > 120)
{
ui8Adjust = 140;
}
else
{
ui8Adjust = 56.0 + ((float) ui8Degrees * (140.0 - 56.0)) / 120.0;

}
PWMPulseWidthSet(PWM0_BASE, PWM_OUT_0, ui8Adjust * ui32Load / 1000); }

//M0 PWM1 Pin PB7 position method
void M0PWM1_PositionServo(uint8_t ui8Degrees, uint32_t ui32Load) // Servo position from 0 to 120 degrees
{
uint8_t ui8Adjust;

if (ui8Degrees > 120)
{
ui8Adjust = 140;
}
else
{
ui8Adjust = 56.0 + ((float) ui8Degrees * (140.0 - 56.0)) / 120.0; }
PWMPulseWidthSet(PWM0_BASE, PWM_OUT_1, ui8Adjust * ui32Load / 1000); }

//M0 PWM2 Pin PB4 position method
void M0PWM2_PositionServo(uint8_t ui8Degrees, uint32_t ui32Load) // Servo position from 0 to 120 degrees
{
uint8_t ui8Adjust;

if (ui8Degrees > 120)
{
ui8Adjust = 140;
}
else
{
ui8Adjust = 56.0 + ((float) ui8Degrees * (140.0 - 56.0)) / 120.0; }
PWMPulseWidthSet(PWM0_BASE, PWM_OUT_2, ui8Adjust * ui32Load / 1000); }
//M0 PWM3 Pin PB5 position method
void M0PWM3_PositionServo(uint8_t ui8Degrees, uint32_t ui32Load) // Servo position from 0 to 120 degrees
{
uint8_t ui8Adjust;

if (ui8Degrees > 120)
{
ui8Adjust = 140;
}
else
{
ui8Adjust = 56.0 + ((float) ui8Degrees * (140.0 - 56.0)) / 120.0; }
PWMPulseWidthSet(PWM0_BASE, PWM_OUT_3, ui8Adjust * ui32Load / 1000); }
//M0 PWM4 Pin PE4 position method void M0PWM4_PositionServo(uint8_t ui8Degrees, uint32_t ui32Load) // Servo position from 0 to 120 degrees
{
uint8_t ui8Adjust;

if (ui8Degrees > 120)
{
ui8Adjust = 140;
}
else
{
ui8Adjust = 56.0 + ((float) ui8Degrees * (140.0 - 56.0)) / 120.0; }
PWMPulseWidthSet(PWM0_BASE, PWM_OUT_4, ui8Adjust * ui32Load / 1000); }
//M0 PWM5 Pin PE5 position method
void M0PWM5_PositionServo(uint8_t ui8Degrees, uint32_t ui32Load) // Servo position from 0 to 120 degrees
{
uint8_t ui8Adjust;

if (ui8Degrees > 120)
{
ui8Adjust = 140;
}
else
{
ui8Adjust = 56.0 + ((float) ui8Degrees * (140.0 - 56.0)) / 120.0; }
PWMPulseWidthSet(PWM0_BASE, PWM_OUT_5, ui8Adjust * ui32Load / 1000); }
//M0 PWM6 Pin PC4 position method
void M0PWM6_PositionServo(uint8_t ui8Degrees, uint32_t ui32Load) // Servo position from 0 to 120 degrees
{
uint8_t ui8Adjust;

if (ui8Degrees > 120)
{
ui8Adjust = 140;
}
else
{
ui8Adjust = 56.0 + ((float) ui8Degrees * (140.0 - 56.0)) / 120.0; }
PWMPulseWidthSet(PWM0_BASE, PWM_OUT_6, ui8Adjust * ui32Load / 1000); }
//M0 PWM7 Pin PC5 position method
void M0PWM7_PositionServo(uint8_t ui8Degrees, uint32_t ui32Load) // Servo position from 0 to 120 degrees
{
uint8_t ui8Adjust;

if (ui8Degrees > 120)

{
ui8Adjust = 140;
}
else
{
ui8Adjust = 56.0 + ((float) ui8Degrees * (140.0 - 56.0)) / 120.0; }
PWMPulseWidthSet(PWM0_BASE, PWM_OUT_7, ui8Adjust * ui32Load / 1000);
}

//------------------------------------------------------------------------------------------------------------
//M1 Position Methods
//-------------------------------------------------------------------------------------------------------------
//M1 PWM0 Pin PD0 position method
void M1PWM0_PositionServo(uint8_t ui8Degrees, uint32_t ui32Load) // Servo position from 0 to 120 degrees
{
uint8_t ui8Adjust;

if (ui8Degrees > 120)
{
ui8Adjust = 140;
}
else
{
ui8Adjust = 56.0 + ((float) ui8Degrees * (140.0 - 56.0)) / 120.0; }
PWMPulseWidthSet(PWM1_BASE, PWM_OUT_0, ui8Adjust * ui32Load / 1000); }

//M1 PWM1 Pin PD1 position method
void M1PWM1_PositionServo(uint8_t ui8Degrees, uint32_t ui32Load) // Servo position from 0 to 120 degrees
{
uint8_t ui8Adjust;

if (ui8Degrees > 120)
{
ui8Adjust = 140;
}
else
{
ui8Adjust = 56.0 + ((float) ui8Degrees * (140.0 - 56.0)) / 120.0; }
PWMPulseWidthSet(PWM1_BASE, PWM_OUT_1, ui8Adjust * ui32Load / 1000); }

//M1 PWM2 Pin PA6 position method
void M1PWM2_PositionServo(uint8_t ui8Degrees, uint32_t ui32Load) // Servo position from 0 to 120 degrees
{
uint8_t ui8Adjust;

if (ui8Degrees > 120)
{
ui8Adjust = 140;
}
else
{
ui8Adjust = 56.0 + ((float) ui8Degrees * (140.0 - 56.0)) / 120.0; }
PWMPulseWidthSet(PWM1_BASE, PWM_OUT_2, ui8Adjust * ui32Load / 1000); }
//M1 PWM3 Pin PA7 position method
void M1PWM3_PositionServo(uint8_t ui8Degrees, uint32_t ui32Load) // Servo position from 0 to 120 degrees
{
uint8_t ui8Adjust;

if (ui8Degrees > 120)
{
ui8Adjust = 140;
}
else
{
ui8Adjust = 56.0 + ((float) ui8Degrees * (140.0 - 56.0)) / 120.0; }
PWMPulseWidthSet(PWM1_BASE, PWM_OUT_3, ui8Adjust * ui32Load / 1000); }
//M1 PWM4 Pin PF0 position method
void M1PWM4_PositionServo(uint8_t ui8Degrees, uint32_t ui32Load) // Servo position from 0 to 120 degrees
{
uint8_t ui8Adjust;

if (ui8Degrees > 120)
{
ui8Adjust = 140;
}
else
{
ui8Adjust = 56.0 + ((float) ui8Degrees * (140.0 - 56.0)) / 120.0; }
PWMPulseWidthSet(PWM1_BASE, PWM_OUT_4, ui8Adjust * ui32Load / 1000); }
//M1 PWM5 Pin PF1 position method
void M1PWM5_PositionServo(uint8_t ui8Degrees, uint32_t ui32Load) // Servo position from 0 to 120 degrees
{
uint8_t ui8Adjust;

if (ui8Degrees > 120)
{
ui8Adjust = 140;
}
else

{
ui8Adjust = 56.0 + ((float) ui8Degrees * (140.0 - 56.0)) / 120.0; }
PWMPulseWidthSet(PWM1_BASE, PWM_OUT_5, ui8Adjust * ui32Load / 1000); }
//M1 PWM6 Pin PF2 position method
void M1PWM6_PositionServo(uint8_t ui8Degrees, uint32_t ui32Load) // Servo position from 0 to 120 degrees
{
uint8_t ui8Adjust;

if (ui8Degrees > 120)
{
ui8Adjust = 140;
}
else
{
ui8Adjust = 56.0 + ((float) ui8Degrees * (140.0 - 56.0)) / 120.0; }
PWMPulseWidthSet(PWM1_BASE, PWM_OUT_6, ui8Adjust * ui32Load / 1000); }
//M1 PWM7 Pin PF3 position method
void M1PWM7_PositionServo(uint8_t ui8Degrees, uint32_t ui32Load) // Servo position from 0 to 120 degrees
{
uint8_t ui8Adjust;

if (ui8Degrees > 120)
{
ui8Adjust = 140;
}
else
{
ui8Adjust = 56.0 + ((float) ui8Degrees * (140.0 - 56.0)) / 120.0; }
PWMPulseWidthSet(PWM1_BASE, PWM_OUT_7, ui8Adjust * ui32Load / 1000); }

A-2) Servo Header File

/*
* servo.h
*
* Created on: Sep 27, 2018
* | Author: jross5
*/

#ifndef SERVO_H_

#define SERVO_H_

extern void delayMS(uint32_t ms);

extern uint32_t getPWMFrequency();
extern uint32_t getPWMClock();
extern uint32_t getLoad(uint32_t ui32PWMClock, uint32_t ui32PWMFreq);

extern void PWM_Enable();
extern void GPIOPWM_Enable();

extern void M0PWM0_Init(uint32_t ui32Load); extern void M0PWM1_Init(uint32_t ui32Load); extern void M0PWM2_Init(uint32_t ui32Load); extern void M0PWM3_Init(uint32_t ui32Load); extern void M0PWM4_Init(uint32_t ui32Load); extern void M0PWM5_Init(uint32_t ui32Load); extern void M0PWM6_Init(uint32_t ui32Load); extern void M0PWM7_Init(uint32_t ui32Load);

extern void M1PWM0_Init(uint32_t ui32Load); extern void M1PWM1_Init(uint32_t ui32Load); extern void M1PWM2_Init(uint32_t ui32Load); extern void M1PWM3_Init(uint32_t ui32Load); extern void M1PWM4_Init(uint32_t ui32Load); extern void M1PWM5_Init(uint32_t ui32Load);
extern void M1PWM6_Init(uint32_t ui32Load);
extern void M1PWM7_Init(uint32_t ui32Load);

extern void M0PWM0_PositionServo(uint8_t ui8Degrees, uint32_t ui32Load); extern void M0PWM1_PositionServo(uint8_t ui8Degrees, uint32_t ui32Load); extern void M0PWM2_PositionServo(uint8_t ui8Degrees, uint32_t ui32Load); extern void M0PWM3_PositionServo(uint8_t ui8Degrees, uint32_t ui32Load); extern void M0PWM4_PositionServo(uint8_t ui8Degrees, uint32_t ui32Load); extern void M0PWM5_PositionServo(uint8_t ui8Degrees, uint32_t ui32Load); extern void M0PWM6_PositionServo(uint8_t ui8Degrees, uint32_t ui32Load); extern void M0PWM7_PositionServo(uint8_t ui8Degrees, uint32_t ui32Load);

extern void M1PWM0_PositionServo(uint8_t ui8Degrees, uint32_t ui32Load); extern void M1PWM1_PositionServo(uint8_t ui8Degrees, uint32_t ui32Load); extern void M1PWM2_PositionServo(uint8_t ui8Degrees, uint32_t ui32Load); extern void M1PWM3_PositionServo(uint8_t ui8Degrees, uint32_t ui32Load);

extern void M1PWM4_PositionServo(uint8_t ui8Degrees, uint32_t ui32Load); extern void M1PWM5_PositionServo(uint8_t ui8Degrees, uint32_t ui32Load); extern void M1PWM6_PositionServo(uint8_t ui8Degrees, uint32_t ui32Load); extern void M1PWM7_PositionServo(uint8_t ui8Degrees, uint32_t ui32Load);

#endif /* SERVO_H_ */

A-3) Legs Code

/*
* legs.c
* Library based off the servo.c that abstracts the control of servos * Created on: Oct 9, 2018
* | Author: jross5
*/

#include <stdint.h>

#include <stdbool.h>

#include "inc/hw_memmap.h" #include "inc/hw_types.h"

#include "driverlib/sysctl.h" #include "driverlib/gpio.h" #include "driverlib/debug.h" #include "driverlib/pwm.h" #include "driverlib/pin_map.h" #include "inc/hw_gpio.h"

#include "driverlib/rom.h"

#include "servo.h"

//------------------------------------------------------------------------------------
//INITIALIZATION METHODS
//------------------------------------------------------------------------------------

//Initialize each PWM pin
void All_PWM_Init(){
uint32_t ui32PWM_Freq = getPWMFrequency(); GPIOPWM_Enable();
PWM_Enable();

// Unlock the Pin PF0 and Set the Commit Bit HWREG(GPIO_PORTF_BASE + GPIO_O_LOCK) = GPIO_LOCK_KEY; HWREG(GPIO_PORTF_BASE + GPIO_O_CR) |= 0x01;

uint32_t ui32PWMClock = getPWMClock();
uint32_t ui32Load = getLoad(ui32PWMClock, ui32PWM_Freq);

M0PWM0_Init(ui32Load); //PB6
M0PWM1_Init(ui32Load); //PB7
M0PWM2_Init(ui32Load); //PB4
M0PWM3_Init(ui32Load); //PB5 M0PWM4_Init(ui32Load); //PE4 M0PWM5_Init(ui32Load); //PE5 M0PWM6_Init(ui32Load); //PC4 M0PWM7_Init(ui32Load); //PC5

M1PWM0_Init(ui32Load); //PD0 M1PWM1_Init(ui32Load); //PD1

M1PWM2_Init(ui32Load); //PA6 M1PWM3_Init(ui32Load); //PA7 M1PWM4_Init(ui32Load); //PF0 M1PWM5_Init(ui32Load); //PF1 M1PWM6_Init(ui32Load); //PF2 M1PWM7_Init(ui32Load); //PF3
}

//Initialize each pin used for the hex's Legs void Legs_Init(uint32_t ui32Load){ GPIOPWM_Enable();
PWM_Enable();
// Unlock the Pin PF0 and Set the Commit Bit HWREG(GPIO_PORTF_BASE + GPIO_O_LOCK) = GPIO_LOCK_KEY; HWREG(GPIO_PORTF_BASE + GPIO_O_CR) |= 0x01;

M0PWM0_Init(ui32Load); //PB6
M0PWM1_Init(ui32Load); //PB7
M0PWM2_Init(ui32Load); //PB4 M0PWM3_Init(ui32Load); //PB5 M0PWM4_Init(ui32Load); //PE4 M0PWM5_Init(ui32Load); //PE5 M0PWM7_Init(ui32Load); //PC5

M1PWM2_Init(ui32Load); //PA6 M1PWM3_Init(ui32Load); //PA7 M1PWM4_Init(ui32Load); //PF0 M1PWM6_Init(ui32Load); //PF2 M1PWM7_Init(ui32Load); //PF3

}

//------------------------------------------------------------------------------------
//LEFT LEG POSITION METHODS //------------------------------------------------------------------------------------

//Front Left Leg position method
//L1F - pin PB5
//L2F - pin PE4
void LegLF_Position(uint8_t ui8L1Degrees,uint8_t ui8L2Degrees,uint32_t ui32Load){
M0PWM3_PositionServo(ui8L1Degrees, ui32Load); M0PWM4_PositionServo(ui8L2Degrees, ui32Load);
}
//Middle Left Leg position method
//L1M - pin PE5
//L2M - pin PB4
void LegLM_Position(uint8_t ui8L1Degrees,uint8_t ui8L2Degrees,uint32_t ui32Load){
M0PWM5_PositionServo(ui8L1Degrees, ui32Load); M0PWM2_PositionServo(ui8L2Degrees, ui32Load);
}

//Back Left Leg position method
//L1B - pin PA6
//L2B - pin PA7
void LegLB_Position(uint8_t ui8L1Degrees,uint8_t ui8L2Degrees,uint32_t ui32Load){
M1PWM2_PositionServo(ui8L1Degrees, ui32Load); M1PWM3_PositionServo(ui8L2Degrees, ui32Load);
}

//------------------------------------------------------------------------------------
//RIGHT LEG POSITION METHODS //------------------------------------------------------------------------------------

//Front Right Leg position method
//R1F - pin PF2
//R2F - pin PF3
void LegRF_Position(uint8_t ui8R1Degrees,uint8_t ui8R2Degrees,uint32_t ui32Load){
M1PWM6_PositionServo(ui8R1Degrees, ui32Load); M1PWM7_PositionServo(ui8R2Degrees, ui32Load);
}
//Middle Right Leg position method
//R1M - pin PF0
//R2M - pin PC5
void LegRM_Position(uint8_t ui8R1Degrees,uint8_t ui8R2Degrees,uint32_t ui32Load){
M1PWM4_PositionServo(ui8R1Degrees, ui32Load); M0PWM7_PositionServo(ui8R2Degrees, ui32Load);
}
//Back right Leg position method
//R1B - pin PB7
//R2B - pin PB6
void LegRB_Position(uint8_t ui8R1Degrees,uint8_t ui8R2Degrees,uint32_t ui32Load){
M0PWM1_PositionServo(ui8R1Degrees, ui32Load); M0PWM0_PositionServo(ui8R2Degrees, ui32Load);
}

//------------------------------------------------------------------------------------
// Custom Position Methods //------------------------------------------------------------------------------------
//Set every servos on body to 60 and servos on legs to 0 degrees. Standing neutrally
void Neutral_Stance(uint32_t ui32Load){
LegLF_Position(60,0,ui32Load);
LegLM_Position(60,0,ui32Load); LegLB_Position(60,0,ui32Load);

LegRF_Position(60,0,ui32Load); LegRM_Position(60,0,ui32Load);

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
A-4) Legs Header File

/*
* legs.h
*
* Created on: Oct 9, 2018
* | Author: jross5
*/

#ifndef LEGS_H_

#define LEGS_H_

extern void All_PWM_Init();
extern void Legs_Init(uint32_t ui32Load);

extern void LegLF_Position(uint8_t ui8L1Degrees,uint8_t ui8L2Degrees,uint32_t ui32Load);
extern void LegLM_Position(uint8_t ui8L1Degrees,uint8_t ui8L2Degrees,uint32_t ui32Load);
extern void LegLB_Position(uint8_t ui8L1Degrees,uint8_t ui8L2Degrees,uint32_t ui32Load);

extern void LegRF_Position(uint8_t ui8R1Degrees,uint8_t ui8R2Degrees,uint32_t ui32Load);
extern void LegRM_Position(uint8_t ui8R1Degrees,uint8_t ui8R2Degrees,uint32_t ui32Load);
extern void LegRB_Position(uint8_t ui8R1Degrees,uint8_t ui8R2Degrees,uint32_t ui32Load);

extern void Neutral_Stance(uint32_t ui32Load);
extern void forward(uint32_t ui32Load, uint32_t delay);
extern void backward(uint32_t ui32Load, uint32_t delay); extern void turn_Right(uint32_t ui32Load, uint32_t delay); extern void turn_Left(uint32_t ui32Load, uint32_t delay); extern void wave_one(uint32_t ui32Load);
extern void wave_two(uint32_t ui32Load);

#endif /* LEGS_H_ */

A-5) UART Code

#include <stdint.h>

#include <stdbool.h>

#include "inc/hw_ints.h"

#include "inc/hw_memmap.h" #include "inc/hw_types.h"

#include "driverlib/gpio.h" #include "driverlib/interrupt.h" #include "driverlib/pin_map.h" #include "driverlib/sysctl.h" #include "driverlib/uart.h"

//Enable UART1 and UART Interrupt //Reciever PB0
//Transmitter PB1
void UART1_Init(){
SysCtlPeripheralEnable(SYSCTL_PERIPH_UART1); GPIOPinConfigure(GPIO_PB0_U1RX); GPIOPinConfigure(GPIO_PB1_U1TX);
GPIOPinTypeUART(GPIO_PORTB_BASE, GPIO_PIN_0 | GPIO_PIN_1);
UARTConfigSetExpClk(UART1_BASE, SysCtlClockGet(), 115200,
(UART_CONFIG_WLEN_8 | UART_CONFIG_STOP_ONE | UART_CONFIG_PAR_NONE));
IntMasterEnable(); //enable processor interrupts
IntEnable(INT_UART1); //enable the UART interrupt
UARTIntEnable(UART1_BASE, UART_INT_RX | UART_INT_RT); //only enable RX and
TX interrupts
}
//Enable UART0 for serial communication via USB
//Reciever PA0
//Transmitter PA1
void UART0_Init(){
SysCtlPeripheralEnable(SYSCTL_PERIPH_UART0); GPIOPinConfigure(GPIO_PA0_U0RX); GPIOPinConfigure(GPIO_PA1_U0TX);
GPIOPinTypeUART(GPIO_PORTA_BASE, GPIO_PIN_0 | GPIO_PIN_1);
UARTConfigSetExpClk(UART0_BASE, SysCtlClockGet(), 115200,
(UART_CONFIG_WLEN_8 | UART_CONFIG_STOP_ONE | UART_CONFIG_PAR_NONE));
}

A-6) UART Header File

/*
* uartcomm.h
*
* Created on: Nov 4, 2018
* | Author: Justin
*/

#ifndef UARTCOMM_H_

#define UARTCOMM_H_

extern void UART1_Init();
extern void UART0_Init();

#endif /* UARTCOMM_H_ */

A-7) Main Code

//Main Code for Tiva
#include <stdint.h>

#include <stdbool.h>

#include "inc/hw_ints.h"

#include "inc/hw_memmap.h" #include "inc/hw_types.h"

#include "driverlib/gpio.h" #include "driverlib/interrupt.h" #include "driverlib/pin_map.h" #include "driverlib/sysctl.h" #include "driverlib/uart.h" #include "servo.h"

#include "legs.h"

#include "uartcomm.h"

char last_Command = 'S';
uint8_t cont_Command = 0;
uint8_t fast_Command = 0;

void UARTIntHandler(void){
uint32_t ui32Status;
char tempChar;

ui32Status = UARTIntStatus(UART1_BASE, true); //get interrupt status

UARTIntClear(UART1_BASE, ui32Status); //clear the asserted interrupts

tempChar = UARTCharGet(UART1_BASE);
if(tempChar == 'C'){
if(cont_Command == 1){
cont_Command = 0;
}else{
cont_Command = 1;
}
}else if(tempChar == 'F'){ if(fast_Command == 1){
fast_Command = 0;
}else{
fast_Command = 1;
}
}else {
last_Command = tempChar;
}
}

int main(void) {
uint32_t ui32PWM_Freq = getPWMFrequency();

SysCtlClockSet(SYSCTL_SYSDIV_4 | SYSCTL_USE_PLL | SYSCTL_OSC_MAIN |
SYSCTL_XTAL_16MHZ);

uint32_t ui32PWMClock = getPWMClock();
uint32_t ui32Load = getLoad(ui32PWMClock, ui32PWM_Freq); Legs_Init(ui32Load);
UART1_Init();

while (1){
switch (last_Command){
case 'S':
Neutral_Stance(ui32Load);
break;
case 'U':
if(fast_Command == 0){
forward(ui32Load, 500);
}else {
forward(ui32Load, 100);
}

if(cont_Command == 0){last_Command = 'S';} break;
case 'D':
if(fast_Command == 0){
backward(ui32Load, 500);
}else {
backward(ui32Load, 100);
}
if(cont_Command==0){last_Command = 'S';} break;
case 'L':
if(fast_Command == 0){
turn_Left(ui32Load, 500);
}else {
turn_Left(ui32Load, 100);
}
if(cont_Command==0){last_Command = 'S';} break;
case 'R':
if(fast_Command == 0){
turn_Right(ui32Load, 500); }else {
turn_Right(ui32Load, 100);
}
if(cont_Command==0){last_Command = 'S';} break;
case 'H':
wave_one(ui32Load);
wave_one(ui32Load);
last_Command = 'S';
break;
case 'W':
wave_two(ui32Load);
wave_two(ui32Load);

last_Command = 'S';
break;
default:
Neutral_Stance(ui32Load);
break;
}
}

}

A-8) tm4c123gh6pm_startup_ccs.c

//***************************************************************************** //
// Startup code for use with TI's Code Composer Studio.
//
// Copyright (c) 2011-2014 Texas Instruments Incorporated. All rights reserved.
// Software License Agreement
//
// Software License Agreement
//
// Texas Instruments (TI) is supplying this software for use solely and // exclusively on TI's microcontroller products. The software is owned by // TI and/or its suppliers, and is protected under applicable copyright // laws. You may not combine this software with "viral" open-source
// software in order to form a larger program.
//
// THIS SOFTWARE IS PROVIDED "AS IS" AND WITH ALL FAULTS.
// NO WARRANTIES, WHETHER EXPRESS, IMPLIED OR STATUTORY, INCLUDING, BUT // NOT LIMITED TO, IMPLIED WARRANTIES OF MERCHANTABILITY AND FITNESS FOR // A PARTICULAR PURPOSE APPLY TO THIS SOFTWARE. TI SHALL NOT, UNDER ANY // CIRCUMSTANCES, BE LIABLE FOR SPECIAL, INCIDENTAL, OR CONSEQUENTIAL
// DAMAGES, FOR ANY REASON WHATSOEVER.
//
//*****************************************************************************

#include <stdint.h>

//***************************************************************************** //
// Forward declaration of the default fault handlers.
//
//***************************************************************************** void ResetISR(void);
static void NmiSR(void);
static void FaultISR(void);
static void IntDefaultHandler(void);

//***************************************************************************** //
// External declaration for the reset handler that is to be called when the // processor is started
//
//***************************************************************************** extern void _c_int00(void);

extern void UARTIntHandler(void); //***************************************************************************** //
// Linker variable that marks the top of the stack.

//
//***************************************************************************** extern uint32_t __STACK_TOP;

//***************************************************************************** //
// External declarations for the interrupt handlers used by the application. //
//***************************************************************************** // To be added by user

//***************************************************************************** //
// The vector table. Note that the proper constructs must be placed on this to // ensure that it ends up at physical address 0x0000.0000 or at the start of // the program if located at a start address other than 0.
//
//***************************************************************************** #pragma DATA_SECTION(g_pfnVectors, ".intvecs")
void (* const g_pfnVectors[])(void) =
{
(void (*)(void))((uint32_t)&__STACK_TOP),
// The initial stack pointer
ResetISR, | // The reset handler
NmiSR, | // The NMI handler
FaultISR, | // The hard fault handler
IntDefaultHandler, | // The MPU fault handler
IntDefaultHandler, | // The bus fault handler
IntDefaultHandler, | // The usage fault handler
0, | // Reserved
0, | // Reserved
0, | // Reserved
0, | // Reserved
IntDefaultHandler, | // SVCall handler
IntDefaultHandler, | // Debug monitor handler
0, | // Reserved
IntDefaultHandler, | // The PendSV handler
IntDefaultHandler, | // The SysTick handler
IntDefaultHandler, | // GPIO Port A
IntDefaultHandler, | // GPIO Port B
IntDefaultHandler, | // GPIO Port C
IntDefaultHandler, | // GPIO Port D
IntDefaultHandler, | // GPIO Port E
IntDefaultHandler, | // UART0 Rx and Tx
UARTIntHandler, | // UART1 Rx and Tx
IntDefaultHandler, | // SSI0 Rx and Tx
IntDefaultHandler, | // I2C0 Master and Slave
IntDefaultHandler, | // PWM Fault
IntDefaultHandler, | // PWM Generator 0
IntDefaultHandler, | // PWM Generator 1
IntDefaultHandler, | // PWM Generator 2
IntDefaultHandler, | // Quadrature Encoder 0
IntDefaultHandler, | // ADC Sequence 0
IntDefaultHandler, | // ADC Sequence 1

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
IntDefaultHandler, | // GPIO Port Q (Summary or Q0)
IntDefaultHandler, | // GPIO Port Q1
IntDefaultHandler, | // GPIO Port Q2
IntDefaultHandler, | // GPIO Port Q3
IntDefaultHandler, | // GPIO Port Q4
IntDefaultHandler, | // GPIO Port Q5
IntDefaultHandler, | // GPIO Port Q6
IntDefaultHandler, | // GPIO Port Q7
IntDefaultHandler, | // GPIO Port R
IntDefaultHandler, | // GPIO Port S
IntDefaultHandler, | // PWM 1 Generator 0
IntDefaultHandler, | // PWM 1 Generator 1
IntDefaultHandler, | // PWM 1 Generator 2
IntDefaultHandler, | // PWM 1 Generator 3
IntDefaultHandler | // PWM 1 Fault
};

//***************************************************************************** //
// This is the code that gets called when the processor first starts execution // following a reset event. Only the absolutely necessary set is performed, // after which the application supplied entry() routine is called. Any fancy // actions (such as making decisions based on the reset cause register, and // resetting the bits in that register) are left solely in the hands of the // application.
//
//***************************************************************************** void
ResetISR(void)
{
//
// Jump to the CCS C initialization routine. This will enable the // floating-point unit as well, so that does not need to be done here. //
__asm(" | .global _c_int00\n"
" | b.w | _c_int00");
}

//***************************************************************************** //
// This is the code that gets called when the processor receives a NMI. This // simply enters an infinite loop, preserving the system state for examination // by a debugger.
//
//***************************************************************************** static void
NmiSR(void)
{
//
// Enter an infinite loop. //
while(1)
{
}

}

//***************************************************************************** //
// This is the code that gets called when the processor receives a fault
// interrupt. This simply enters an infinite loop, preserving the system state // for examination by a debugger.
//
//***************************************************************************** static void
FaultISR(void)
{
//
// Enter an infinite loop. //
while(1)
{
}
}

//***************************************************************************** //
// This is the code that gets called when the processor receives an unexpected // interrupt. This simply enters an infinite loop, preserving the system state // for examination by a debugger.
//
//***************************************************************************** static void
IntDefaultHandler(void)
{
//
// Go into an infinite loop. //
while(1)
{
}
}

A-9) NodeMCU Code

//Code for Hexapod Capstone Controller //Written for NODEMCU
#include <ESP8266WiFi.h>

#include <WiFiClient.h>

#include <ESP8266WebServer.h> #include "index.h"

const char *ssid = "CAPSTONE";
const char *password = "SUNY2018";
const int max_connection = 1;

String header = "HTTP/1.1 200 OK\r\nContent-Type: text/html\r\n\r\n"; String page = MAIN_page;
String request = "";

WiFiServer server(80);

void setup() {
Serial.begin(115200);
WiFi.softAP(ssid, password,max_connection); IPAddress myIP = WiFi.softAPIP(); server.begin();
}

void loop() {
WiFiClient client = server.available(); if (!client) {
return;
}
request = client.readStringUntil('\r');

if ( request.indexOf("STOP") > 0 ) { Serial.print('S');
client.print( header );
client.print( "Stop was Pressed" ); }else if ( request.indexOf("UP") > 0 ) { Serial.print('U');
client.print( header );
client.print( "Up was Pressed" ); }else if ( request.indexOf("DOWN") > 0 ) { Serial.print('D');
client.print( header );
client.print( "Down was Pressed" ); }else if ( request.indexOf("LEFT") > 0 ){ Serial.print('L');
client.print( header );
client.print( "Left was Pressed" ); }else if ( request.indexOf("RIGHT") > 0 ) { Serial.print("R");
client.print( header );
client.print( "Right was Pressed" );

}else if ( request.indexOf("HELLO") > 0 ) { Serial.print("H");
client.print( header );
client.print( "Hello World!" ); }else if (request.indexOf("WAVE") > 0) { Serial.print("W");
client.print( header );
client.print( "Hello World!" ); }else if (request.indexOf("CONT") > 0){ Serial.print("C");
client.print( header );
}else if (request.indexOf("FAST") > 0){ Serial.print("F");
client.print( header );
client.print( "RB" );
}else {
client.flush();
client.print( header );
client.print( page );
delay(5);
}
}

A-10)Index.h

const char MAIN_page[] PROGMEM = R"=====( <!DOCTYPE html>
<html>
<head>
<meta name='viewport' content='width=device-width, initial-scale=1.0'/> <meta charset='utf-8'>

<style>

.base-grid{
display: grid;
grid-template-columns: auto auto; grid-template-rows: auto auto; }

.grid-container {
display: grid;
grid-gap: 10px 10px;
grid-template-columns: auto auto auto; background-color: #FFFFFF;
padding: 10px;
}

.grid-item {
background-color: rgba(255, 255, 255, 255); font-size: 30px;
text-align: center;
}
.grid-item2 {
background-color: rgba(255, 255, 255, 255); text-align: left;
}

.button {
background-color: #efefef; /* Gray */ border: 2px solid black;
border-radius: 8px;
color: black;
padding: 10px;
text-align: center;
text-decoration: none;
display: inline-block;
font-size: 30px;
margin: 4px 2px;
cursor: pointer;
}
.panicbutton {
background-color: #ff0000; /* RED */ border: 2px solid black;
border-radius: 8px;

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
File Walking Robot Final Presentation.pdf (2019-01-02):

# Hexapod Walking Robot

Kara Fortunato
Justin Ross
Justin Purtell

# Problem Statement

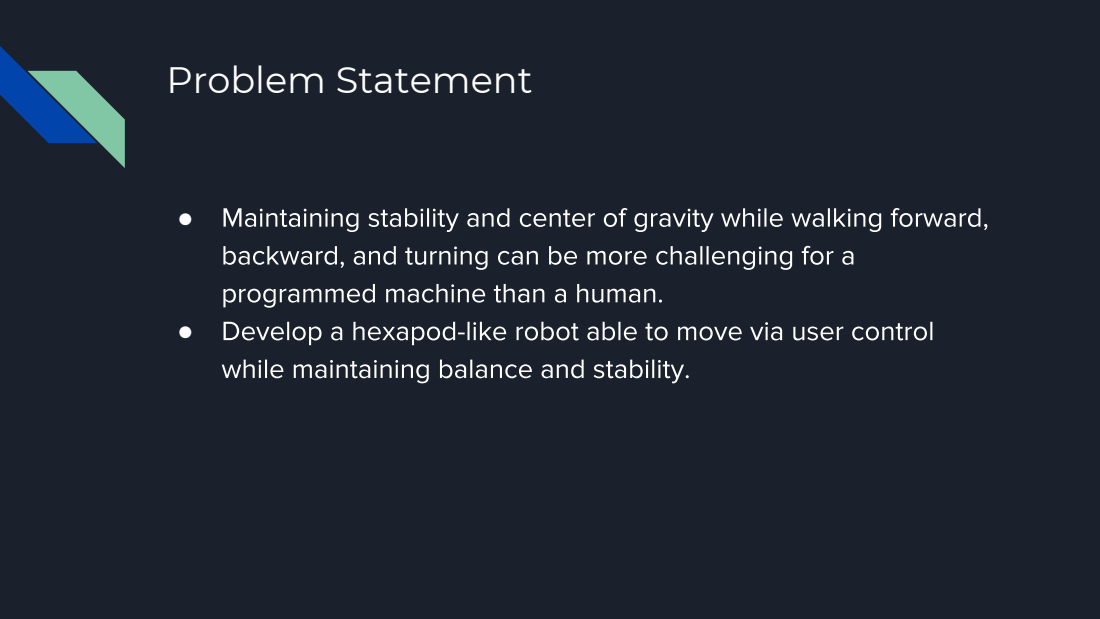
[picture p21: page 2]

# Overview

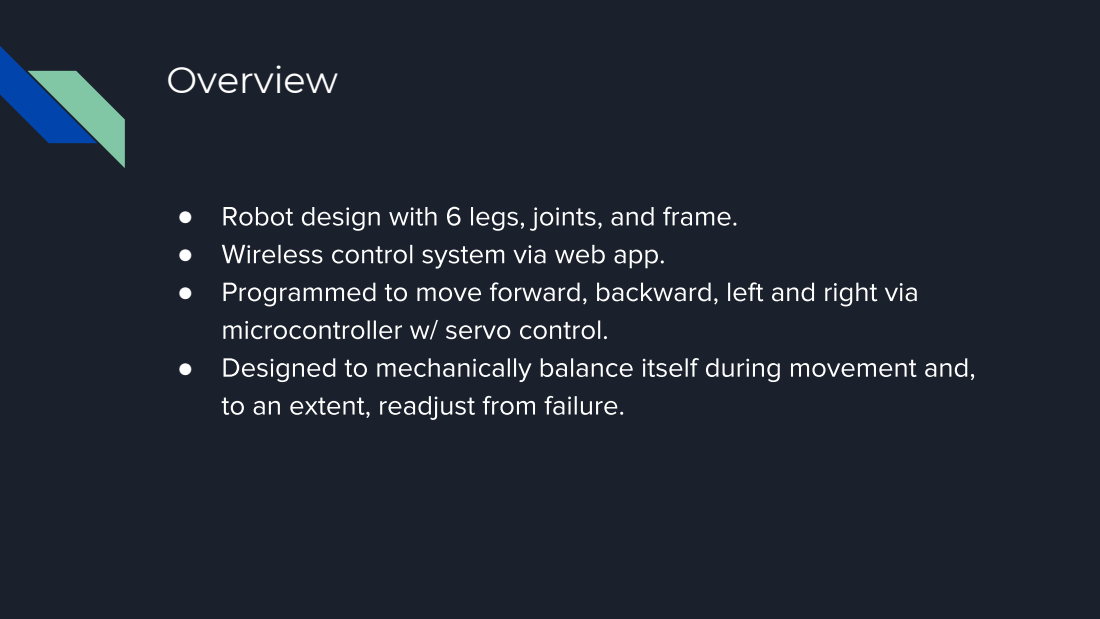
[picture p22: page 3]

# Parts List

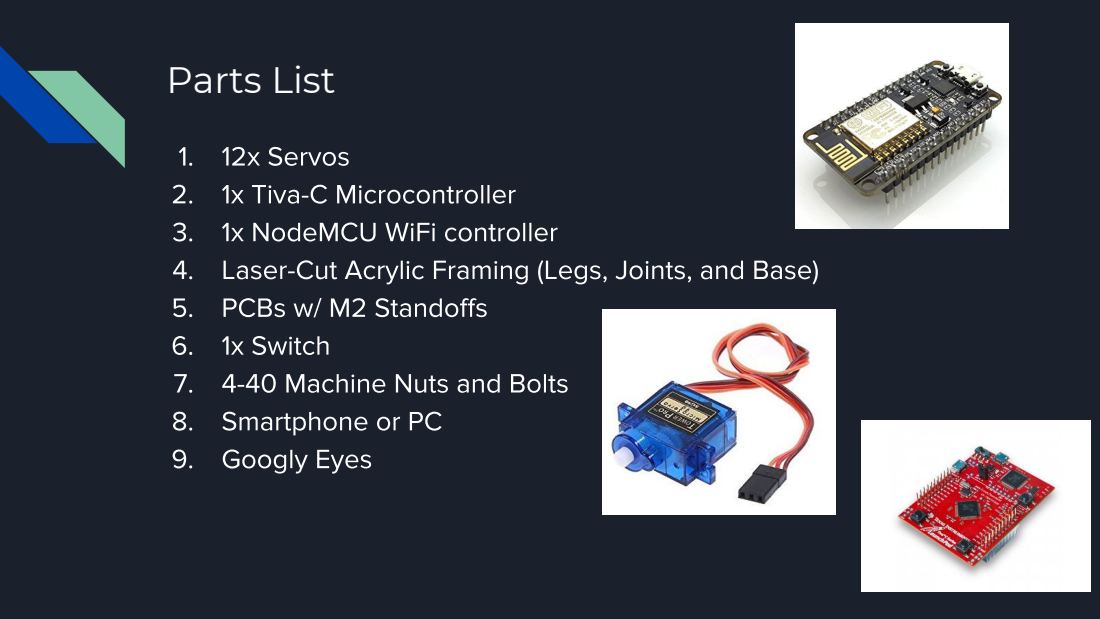
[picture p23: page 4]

# TM4C123GH6PM

●

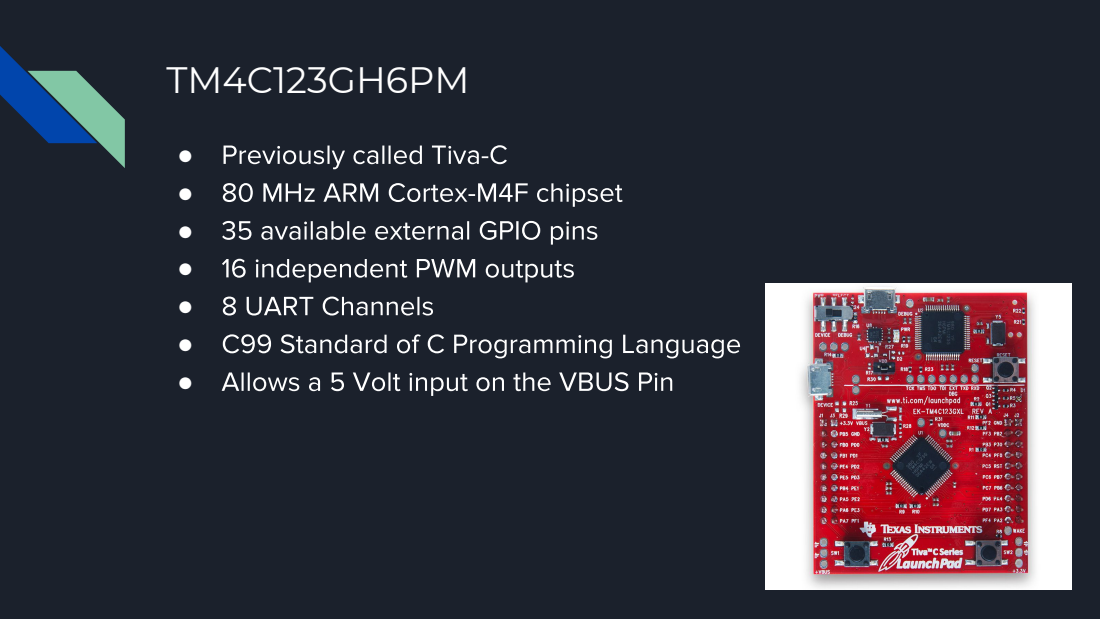
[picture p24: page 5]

# SG90 Servos

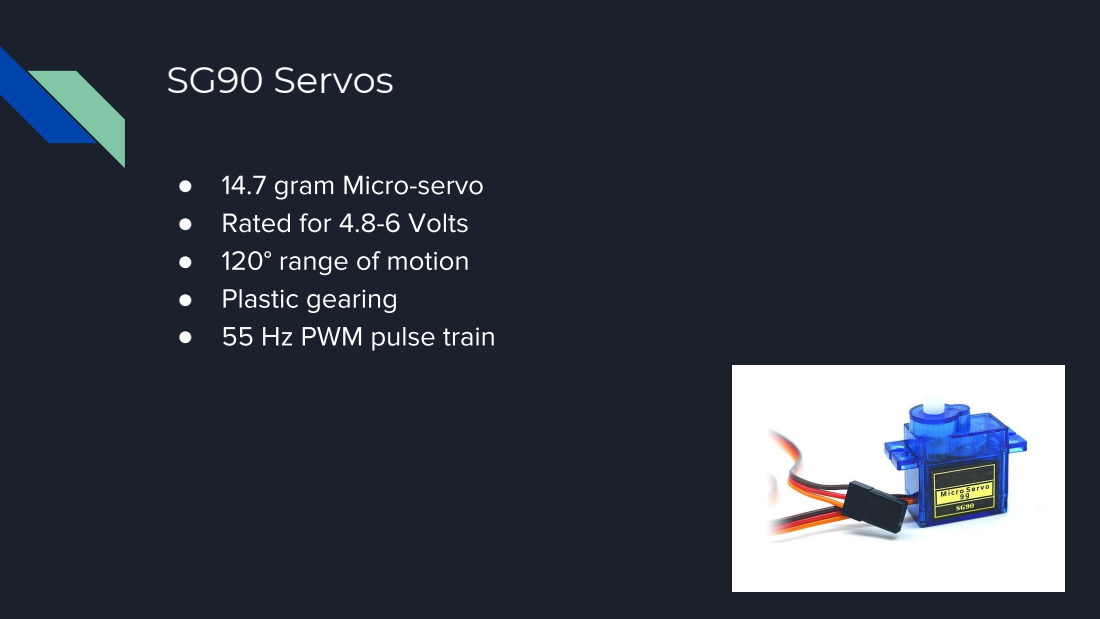
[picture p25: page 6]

# NodeMCU

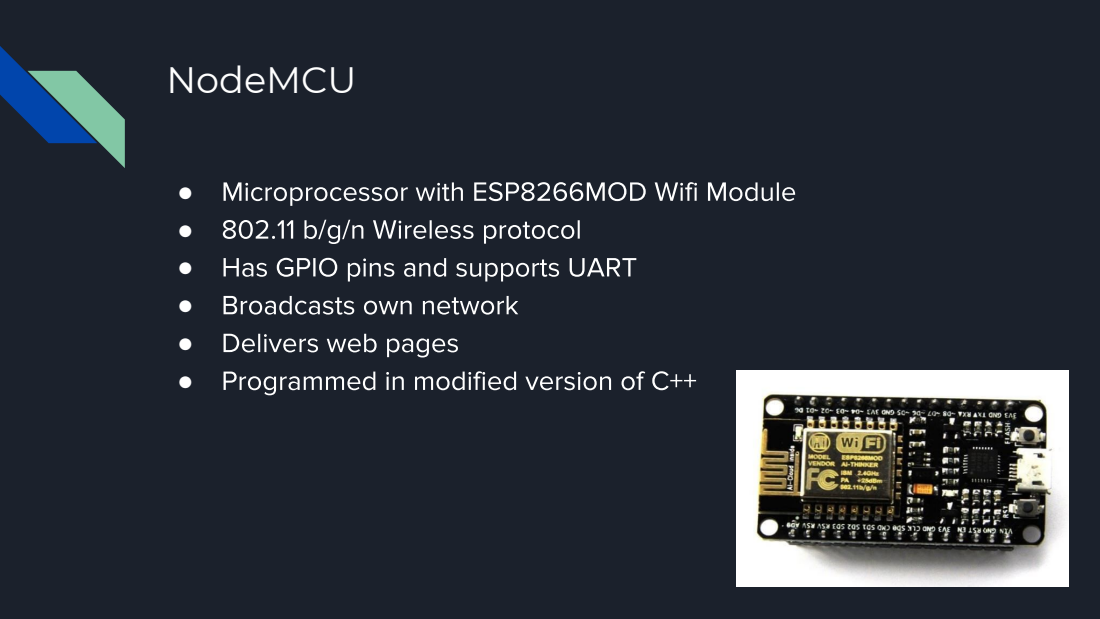
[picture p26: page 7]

# The Body

●


# The Body (Cont.)


# The Body (Cont.)


# The Body (Cont.)


# Tripod Gait


# Circuit


# Web App Controller

●


# Cost Analysis


# Work Process


# Video


# Want to name it? Take our Survey

## https://goo.gl/forms/k4L7yxuELGz0Iumn2

# References

References

[1]B. Baxter, “Tripod-walking Gait,” The Tripod Gait as a Model for Robots. [Online]. Available: https://tripodgaitasamodelforrobots.weebly.com/tripod-walking-gait.html.

[2]“Tiva™ TM4C123GH6PM Microcontroller,” ti.com. [Online]. Available: http://www.ti.com/lit/ds/symlink/tm4c123gh6pm.pdf.

[3]“SG90 Data Sheet.” [Online]. Available: http://www.ee.ic.ac.uk/pcheung/teaching/DE1_EE/stores/sg90_datasheet.pdf.

[4]“NodeMCU ESP8266 ESP-12E WiFi Development Board.” [Online]. Available: https://einstronic.com/wp-content/uploads/2017/06/NodeMCU-ESP8266-ESP-12E-Catalogu e.pdf.

# Any Questions?

Thank you for your attention!

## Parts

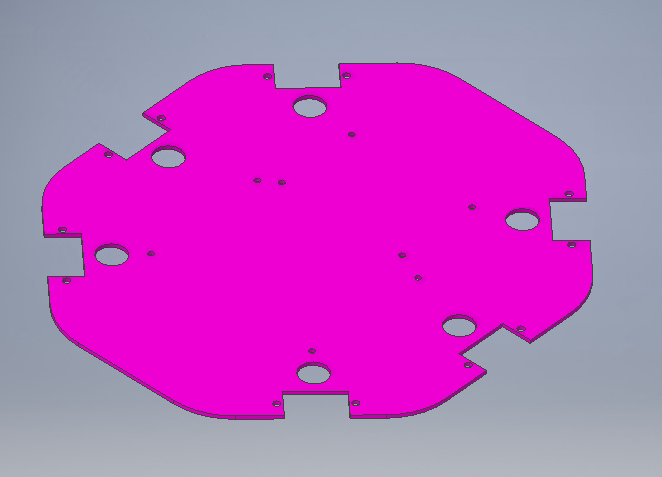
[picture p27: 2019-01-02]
Inventor Parts/Pictures of Parts/Base.PNG

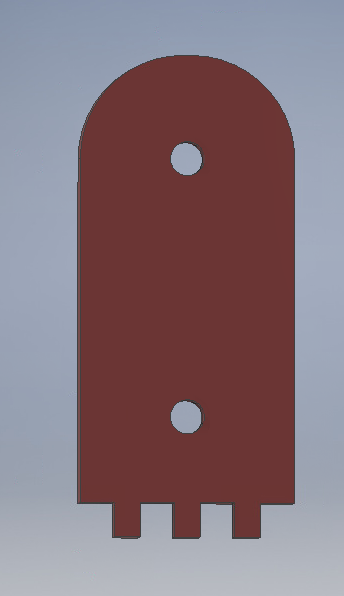
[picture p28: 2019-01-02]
Inventor Parts/Pictures of Parts/Connection4.PNG

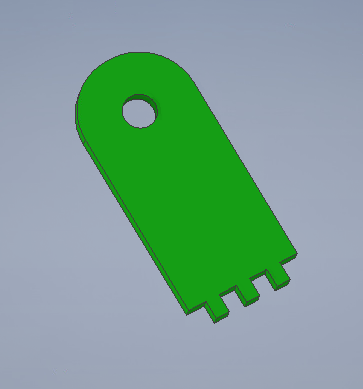
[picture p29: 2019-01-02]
Inventor Parts/Pictures of Parts/connection4-3.5.PNG

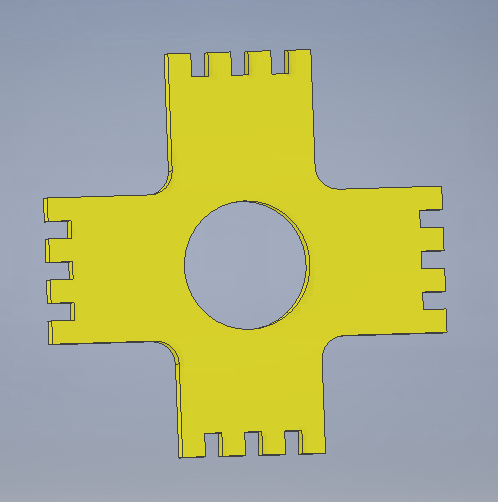
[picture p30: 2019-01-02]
Inventor Parts/Pictures of Parts/Cross.PNG

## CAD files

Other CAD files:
FinalDrawing.dwg
Inventor Parts/Base.ipt
Inventor Parts/Connection4-3.5.ipt
Inventor Parts/Connection4.ipt
Inventor Parts/Servo.ipt
Inventor Parts/cross.ipt
Inventor Parts/legAssembly.iam
Inventor Parts/legRound.ipt
Inventor Parts/screwLarge.ipt
Inventor Parts/screwSmall.ipt
Inventor Parts/withBase.iam

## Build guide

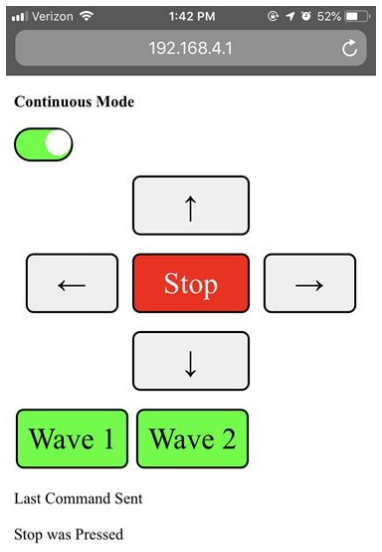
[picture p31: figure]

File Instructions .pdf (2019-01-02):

Turn on the robot by connecting it to a 5 Volt 3 Amp source

Wait for the NodeMCU WiFi board to boot up, this can take up to a minute.
Once booted up, use any WiFi enabled device to join the CAPSTONE network with password SUNY 2018
SSID: CAPSTONE
PASS: SUNY2018

Once connected, navigate to your web browser of choice. In the address bar type 192.168.4.1 and hit enter.

The Up button moves the robot forward. The Down button moves the robot backward The Left button turns the robot left
The Right button turns the robot right
The Stop button stops the robot
The Wave 1 button waves one leg
The Wave 2 button waves two legs

The continuous switch allows to switch on and off continuous mode. When the robot is in continuous mode, the last button pressed will keep running until another button is pressed, with the exception of the two wave functions. When the robot is not in continuous mode, each press of the button calls one cycle of that method, and then stops.
